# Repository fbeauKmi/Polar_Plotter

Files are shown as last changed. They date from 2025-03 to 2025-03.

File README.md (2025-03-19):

# Polar Plotter



Experimental plotter. It runs under Kalico and uses klipper polar kinematics.

Polar plotter is driven by [VØ](https://github.com/fbeauKmi/v-nothing)

## Bill of Materials

| **Hardware** | **Quantity** | **Notes** |
|---|---|---|
| Stepper Nema17 | 2 | |
| Servo Savox SH0255 or M90s | 1 | |
| Linear Rail MGN9C 150mm  | 1 | |
| Open Belt GT2 6mm 514mm  | 1 | |
| Loop Belt GT2 6mm 300mm  | 1 | |
| GT2 Gear 20T 6mm | 2 | |
| Bearing F623zz | 8 | |
| Bearing F695zz | 2 | |
| Rod D3mm 75mm | 2 | Sourced from an old DVD writer |
| BHCS, SHCS M3/M5 Screws & Nuts | - | Minimal quantity required |
| SBC and MCU | 1 | Use a [VØ](https://github.com/fbeauKmi/v-nothing) |
| Permanent marker | 1 | [Sharpie Ultrathin](https://www.amazon.com/Sharpie-37001-Permanent-Markers-Ultra/dp/B00006IFI7) or [Staedler Lumocolor 313](https://www.amazon.de/-/en/Staedtler-313-WP4-Universal-Lumocolor/dp/B0007OEDQQ) | 

## G0 macro override
To avoid crossing 0,0
G1 moves (drawing) are "linear" and G0 moves (travel) are polar

see [printer.cfg](./config/kalico/config/printer.cfg) for configuration

## Write G-Code from SVG
### Draw your model with Inkscape
Kinematic size is 120mm in diameter
Use model [DVD_label.svg](./config/svg/DVD_label.svg) as example

Extensions like Eggbot Hatch fill or Hershey Text can be useful for a plotter use

### KPolar
I use [KPolar](https://github.com/fbeauKmi/KPolar) a fork of [GRBL-Plotter](https://github.com/svenhb/GRBL-Plotter)
to convert SVG into gcode and send it to the plotter via Moonraker API.

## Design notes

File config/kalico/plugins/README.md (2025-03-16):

- install [vars.py](https://github.com/fbeauKmi/kbobine_filament_settings/blob/develop/klipper/klippy/plugins/vars.py) in ~/klipper/klippy/plugins

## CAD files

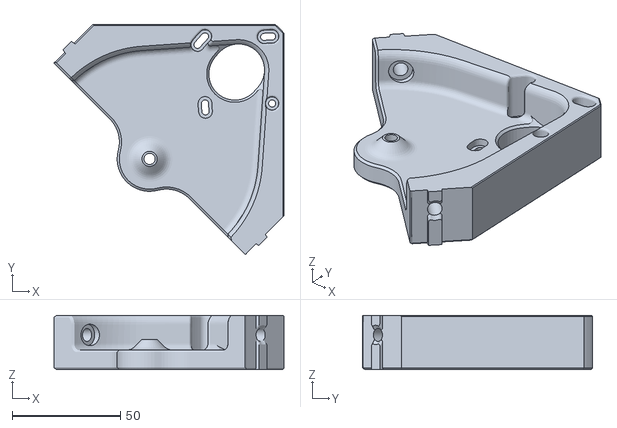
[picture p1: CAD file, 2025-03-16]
STL/Main_body.stl
106.3 x 106.3 x 25.0

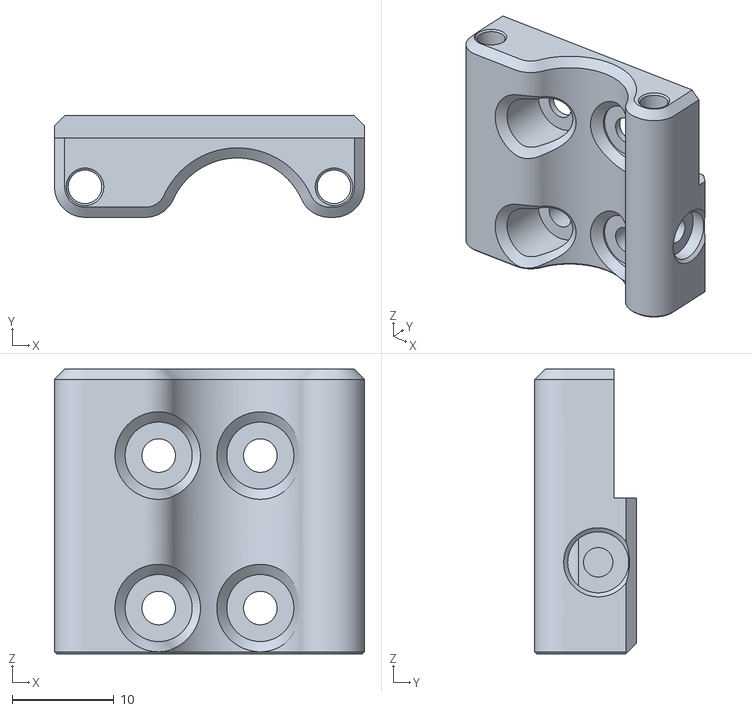
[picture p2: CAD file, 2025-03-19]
STL/MGN9_mount.stl
30.5 x 10.0 x 28.0

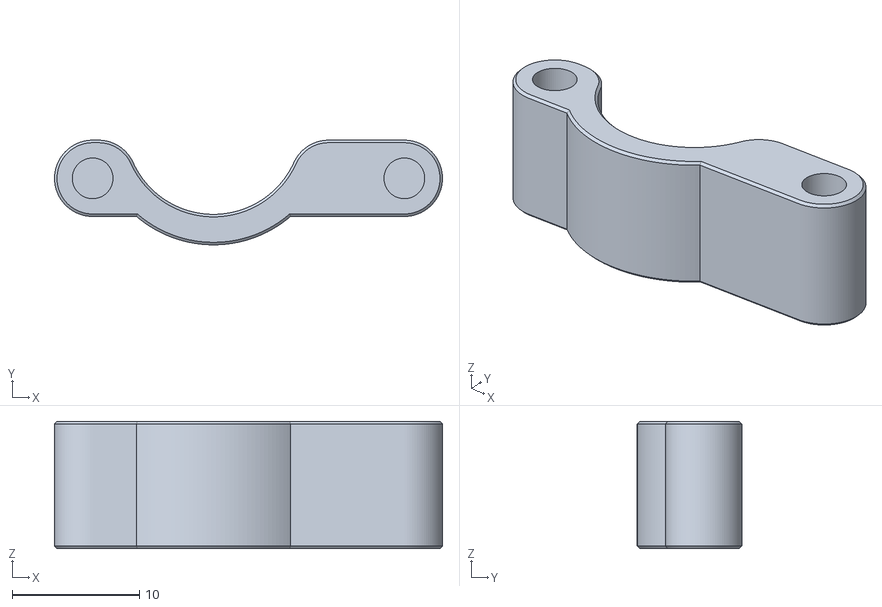
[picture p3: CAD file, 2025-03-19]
STL/rod_holder.stl
30.5 x 8.23 x 10.0

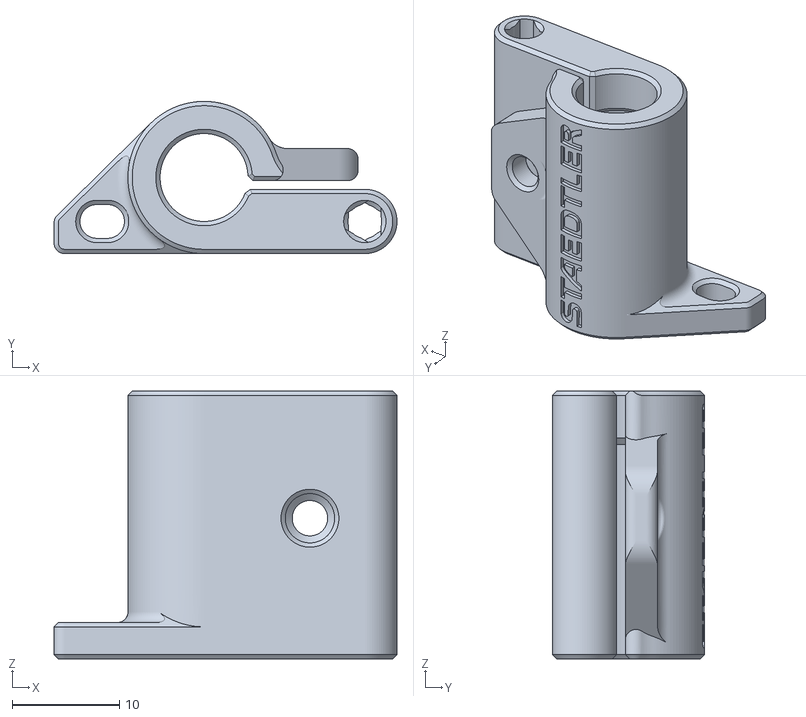
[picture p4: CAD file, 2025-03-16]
STL/slider_staedler.stl
32.0 x 14.2 x 25.0

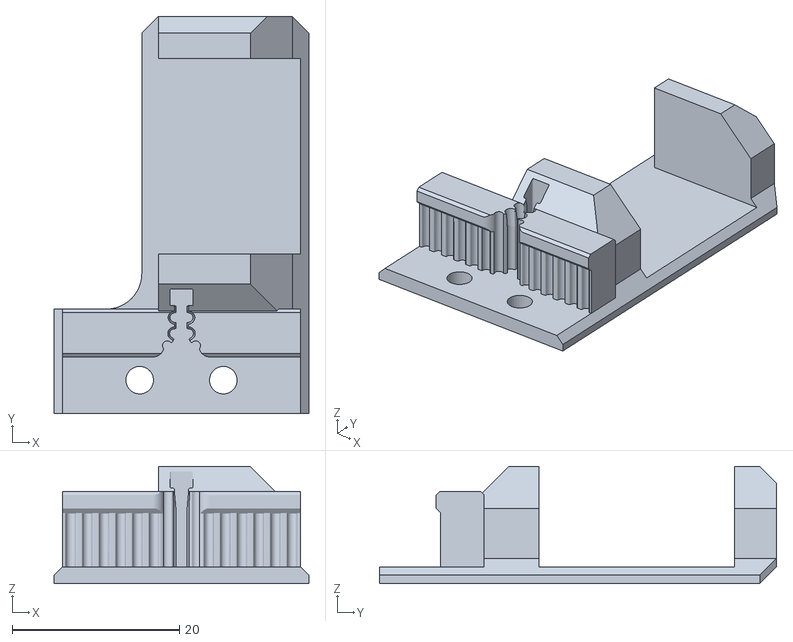
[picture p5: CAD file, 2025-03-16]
STL/belt_servo_holder.stl
30.5 x 47.5 x 14.0

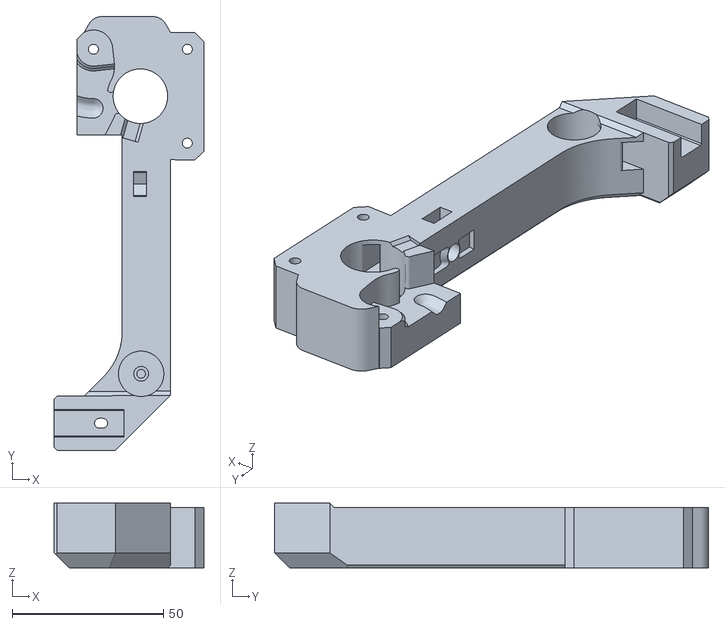
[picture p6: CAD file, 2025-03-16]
STL/right_arm.stl
49.5 x 143.3 x 21.4

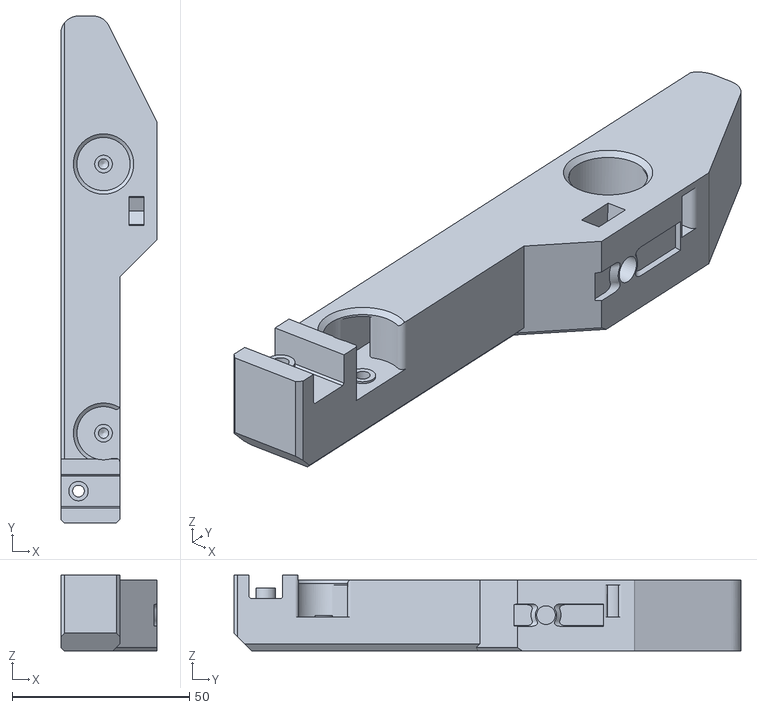
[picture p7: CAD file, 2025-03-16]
STL/left_arm.stl
27.2 x 143.0 x 21.4

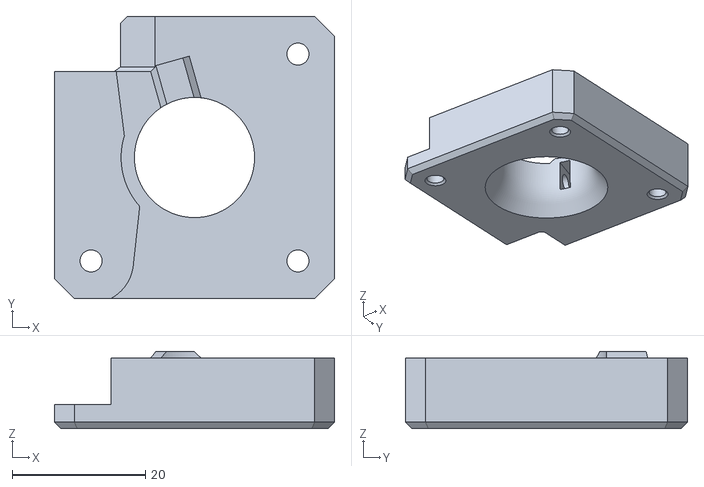
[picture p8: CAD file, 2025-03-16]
STL/x-stepper spacer.stl
42.0 x 42.3 x 11.6

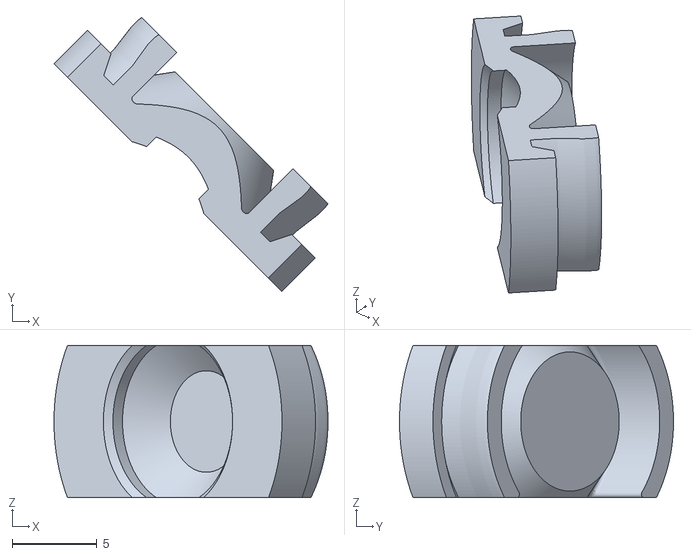
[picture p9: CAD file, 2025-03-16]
STL/cap.stl
16.2 x 16.2 x 9.00

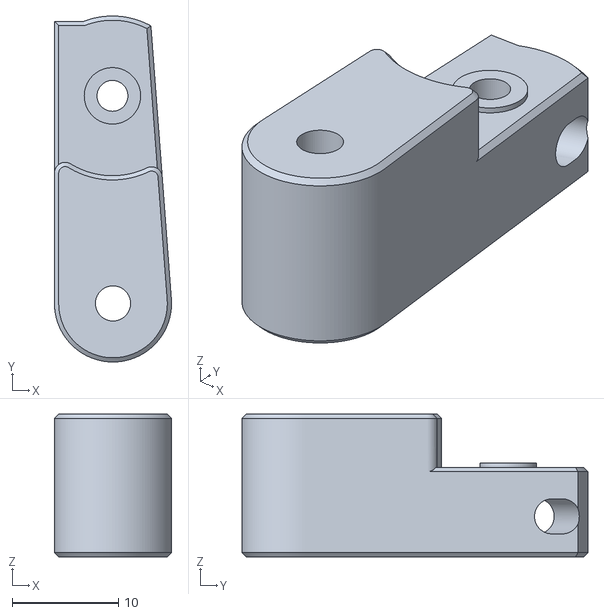
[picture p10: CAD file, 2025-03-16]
STL/tensioner.stl
11.0 x 32.5 x 13.4

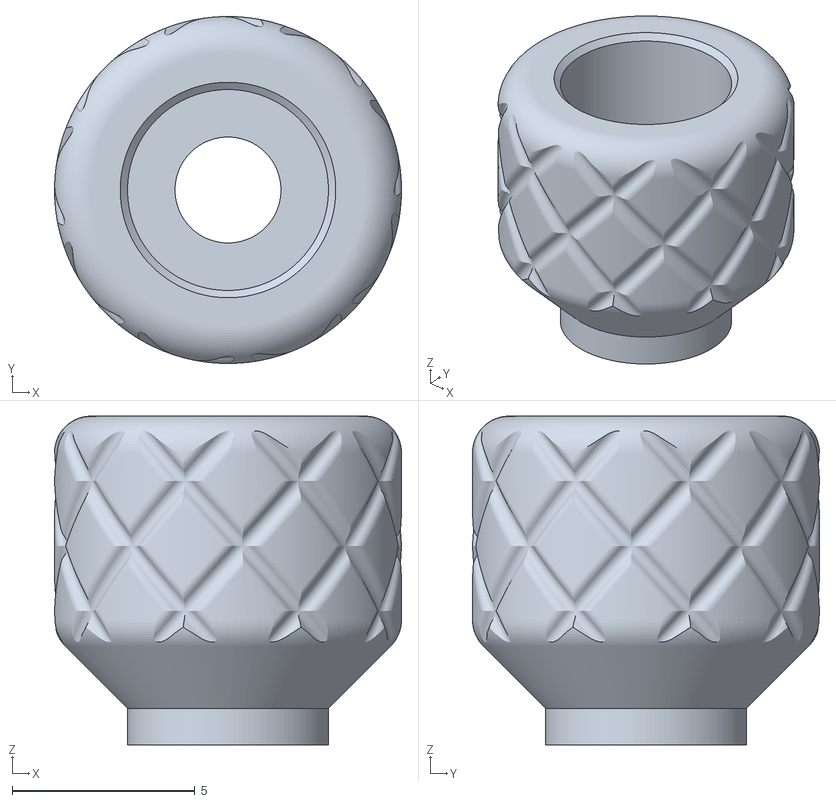
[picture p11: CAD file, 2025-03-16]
STL/screw_head.stl
9.50 x 9.50 x 9.00

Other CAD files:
STL/slider_sharpie_ufp.stl

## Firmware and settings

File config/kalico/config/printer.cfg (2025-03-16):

##  Disk Labeller config file
## author : fboc
# Licence under GPL 3.0

[include fluidd.cfg]

[printer]
kinematics: polar
max_velocity: 1000
max_accel: 5000

[mcu]
serial: <your serial here>
#restart_method : command

[sdcard_loop]
[respond]

# Polar disk holder
[stepper_bed]
step_pin: MOTOR0_STEP
dir_pin: MOTOR0_DIR
enable_pin: !MOTOR0_ENABLE
microsteps: 32
gear_ratio: 140:20

[tmc2209 stepper_bed]
uart_pin: MOTOR0_UART
run_current: 0.8
sense_resistor: 0.11

[tmc2209 stepper_arm]
diag_pin: ^DIAG1
uart_pin: MOTOR1_UART
run_current: 0.8
home_current: 0.5
sense_resistor: 0.11
driver_SGTHRS: 110

[stepper_arm]
step_pin: MOTOR1_STEP
dir_pin: MOTOR1_DIR
enable_pin: !MOTOR1_ENABLE
microsteps: 32
endstop_pin: tmc2209_stepper_arm:virtual_endstop
position_endstop: 60
position_max: 60
homing_speed: 70
second_homing_speed: 70
homing_retract_dist: 5
min_home_dist: 10
rotation_distance: 40

# Fake stepper Z otherwise polar kinematic won't work
[stepper_z]
step_pin: MOTOR2_1_STEP
dir_pin: MOTOR2_1_DIR
enable_pin: !MOTOR2_1_ENABLE
microsteps: 32
endstop_pin: !DIAG2
rotation_distance: 40
position_endstop: 0
position_max: 10

[tmc2209 stepper_z]
uart_pin: MOTOR2_1_UART
run_current: 0.8
sense_resistor: 0.11

# Homing override, disable z stepper
[homing_override]
axes: yxz
set_position_z: 0
gcode:
    PEN_UP
    G28 X
    _CHECK_HOMED

[gcode_macro _CHECK_HOMED]
gcode:
    {% if "xyz" in printer.toolhead.homed_axes %}
        {% set arm=printer.configfile.config.stepper_arm %}
        SET_KINEMATIC_POSITION X={arm.homing_retract_dist|default(10)|float - arm.position_endstop|float}
    {% endif %}

[servo pencil]
pin: SERVOS
maximum_servo_angle: 180
minimum_pulse_width: 0.00085
maximum_pulse_width: 0.00215

# Pencil control macros
[vars PENCIL]
base_angle: 62
count_loop: 1


[gcode_macro PEN_UP]
gcode:

    SET_SERVO SERVO=pencil ANGLE={printer.vars.PENCIL.base_angle - 20}
    G4 P120

[gcode_macro PEN_DOWN]
gcode:
    
    SET_SERVO SERVO=pencil ANGLE={printer.vars.PENCIL.base_angle}
    G4 P50

[gcode_macro CHANGE_PENCIL_HOLDER]
gcode:
    PAUSE
    SET_SERVO SERVO=pencil ANGLE=130
    SET_SERVO SERVO=pencil WIDTH=0
    G4 P1000

[gcode_macro SET_GCODE_OFFSET]
rename_existing: SET_GCODE_OFFSET_BASE
gcode:
    {% if "Z_ADJUST" in params %}
        {% set z_adjust = params.Z_ADJUST|float * 200 %}
        SET_VARS_PENCIL BASE_ANGLE={printer.vars.PENCIL.base_angle - z_adjust} PERSISTENT=1
        PEN_UP
        G4 P200
    {% endif %}

[gcode_macro G0]
rename_existing: G0.1
gcode:
    # G0 fast moves (deplacement only) are transformed to polar moves to avoid
    # crossing 0,0 and stupidly fast bed accel/speed around it  

    {% set speed=params.F|default(printer.gcode_move.speed)|float %} 
    {% set x1, y1 , _, _ = printer.gcode_move.position %}
    {% set x2, y2 = params.X|default(x1)|float, params.Y|default(y1)|float %}
    {% set r1 = math.sqrt(x1**2 + y1**2) %}
    {% set theta1 = math.atan2(x1, y1) %}
    {% set r2 = math.sqrt(x2**2 + y2**2) %}
    {% set theta2 = math.atan2(x2, y2) %}

    {% if theta2 - theta1 > math.pi %}
        {% set theta2 = theta2 - math.pi*2 %}
    {% elif theta2 - theta1 < - math.pi %}
        {% set theta2 = theta2 + math.pi*2 %}
    {% endif %}

    {% set nb_segment = math.floor((r1 + r2) * math.fabs(theta2 - theta1) / 2) %}
    {% if nb_segment > 0 %}
        {% set dtheta=(theta2 - theta1)/nb_segment %}
        {% set dr=(r2 - r1)/nb_segment %}
        {% for i in range(1 , nb_segment) %}
            {% set x = (r1 + i * dr ) * math.sin (theta1 + i * dtheta) %}
            {% set y = (r1 + i * dr ) * math.cos (theta1 + i * dtheta) %} 
            G0.1 {"X%.3f Y%.3f" % (x,y)} F{speed * (r1 + i * dr ) / 20}
        {% endfor %}
    {% endif %}
    G0.1 {"X%.3f Y%.3f" % (x2,y2)} F{speed}

# Remove unused gcodes
[gcode_macro M30]
rename_existing: M30.1
gcode: M84

[gcode_macro M84]
rename_existing: M84.1
gcode:
    SET_SERVO SERVO=pencil WIDTH=0
    M84.1

# Loop setting
[gcode_macro MULTI_DISK]
gcode:
    SET_VARS_PENCIL COUNT_LOOP={params.COUNT|default(1)}
    _PP_RESPOND MSG="MULTI_DISK : {params.COUNT|default(1)} Disk(s) to print"

# PP Respond
[gcode_macro _PP_RESPOND]
gcode:
    RESPOND PREFIX='Polar Pencil Plotter' MSG="<span class="warning"--text>{params.MSG}</span>"

# Start helper
[gcode_macro CANCEL_PRINT]
rename_existing: CANCEL_PRINT_BASE
gcode:
    SET_VARS_PENCIL COUNT_LOOP=1
    CANCEL_PRINT_BASE
    PEN_UP
    END_PRINT
    M30

[gcode_macro START_PRINT]
gcode:
    {% if printer.vars.PENCIL.count_loop > 1 %}
    _PP_RESPOND MSG="{printer.vars.PENCIL.count_loop}  disk(s) to print"
    SDCARD_LOOP_BEGIN COUNT={printer.vars.PENCIL.count_loop}
    {% endif %}
    G28
    G0 F5000

[gcode_macro END_PRINT]
gcode:
    G4 P500
    G0 X-55 Y0
    {% if printer.vars.PENCIL.count_loop > 1 %}
        PAUSE
        SET_VARS_PENCIL COUNT_LOOP={printer.vars.PENCIL.count_loop - 1}
        _PP_RESPOND MSG="{printer.vars.PENCIL.count_loop - 1}  disk(s) remaining"
        RESPOND PREFIX="   " MSG="Add new disk and press RESUME"
        SDCARD_LOOP_END
    {% endif %}

    

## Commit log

2025-03-19 new MGN9 mount
    [MGN9_mount.stl, rod_holder.stl]
2025-03-19 Add BOM
2025-03-20 CAD : add hardware
